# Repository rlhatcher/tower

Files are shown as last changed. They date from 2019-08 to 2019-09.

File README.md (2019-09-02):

# Launch Tower
This is a (mostly) printed Launch Tower for model rockets. The length is 1m, which is _not_ optimal (1.5m would be best) but the tubes I wanted to use come in 1m or 2m lengths so ...

Rather than work through the complications of desinging an adjustable tower, different size rockets can be accomodated by printing approriate sized upper and lower mounts. 15mm and 20mm body diameter .STLs are provided along with the source [Fusion 360 design file](https://github.com/rlhatcher/tower/blob/master/Tower%20Launcher.f3d?raw=true) where the parameters can be easilly adjusted for any size.

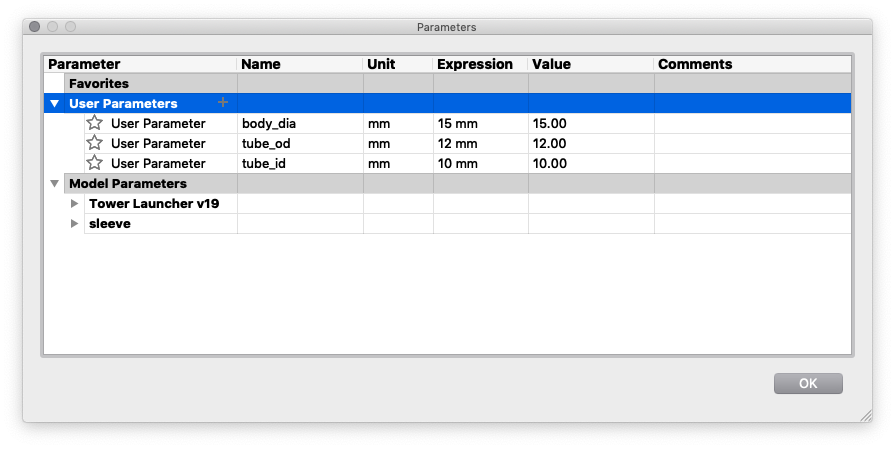
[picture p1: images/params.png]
Parameters


The original design had printed "pegs" on the bottom mount, which promptly bronke on the first attempted use. In hindsight, breaking was inevitble due to the printing orientation so the revied design uses wooden dowels instead. As is often the case, this led to another problem in that 10mm dowelling is _impossible_ to source locally so 8mm dowel with a printed "sleeve" to bring the OD to 10mm and prvide a sung fit with the tubes.



## Ingredients

### Printed

* 3X legs
* Base plate
* 3X dowell sleeves
* Lower mounting plate
* Upper mounting sleeve

### Non-printed

* 3X 8mm multi-groove dowel (40mm long)
* 3X Carbon fibre tubes 12mmx10mmx1m [like these](https://www.easycomposites.co.uk/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)
 
# Assembly

Start with the three legs and the base 

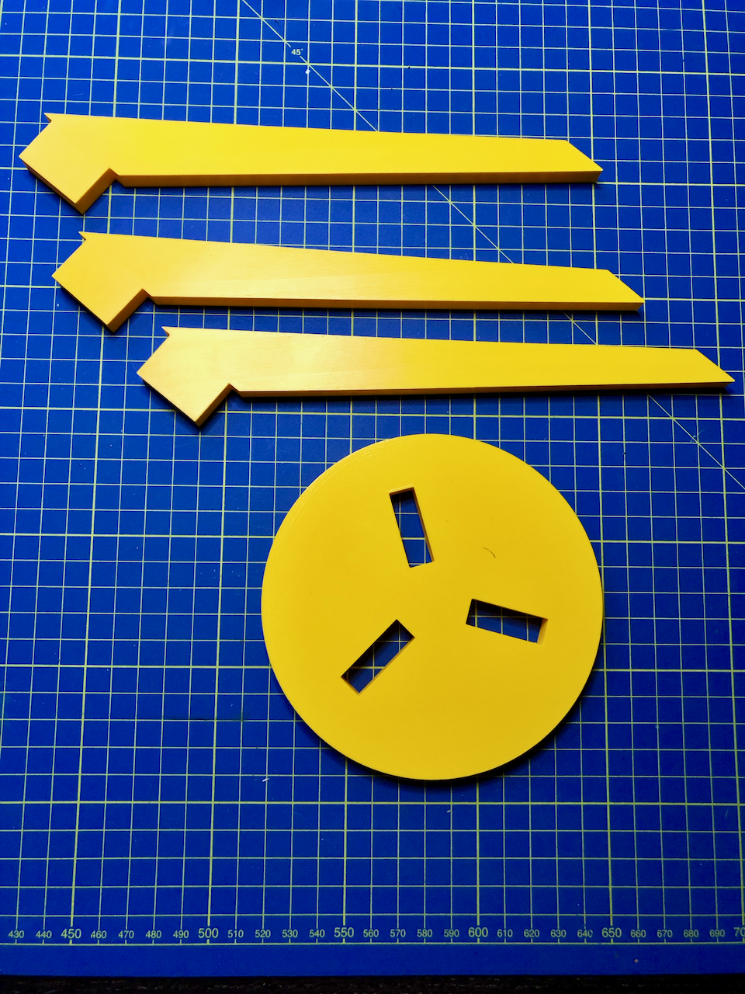
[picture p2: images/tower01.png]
Base


Simply snap the legs throguh the base

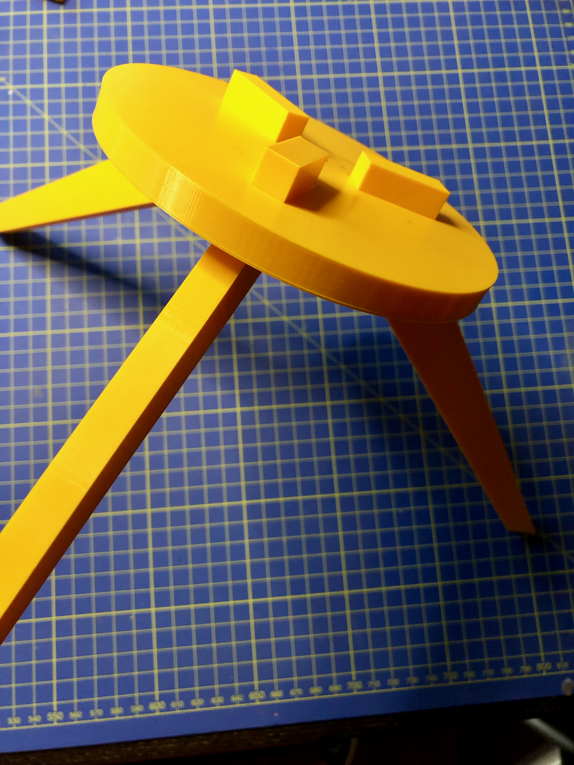
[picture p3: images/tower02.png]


Take the lower mounting plate

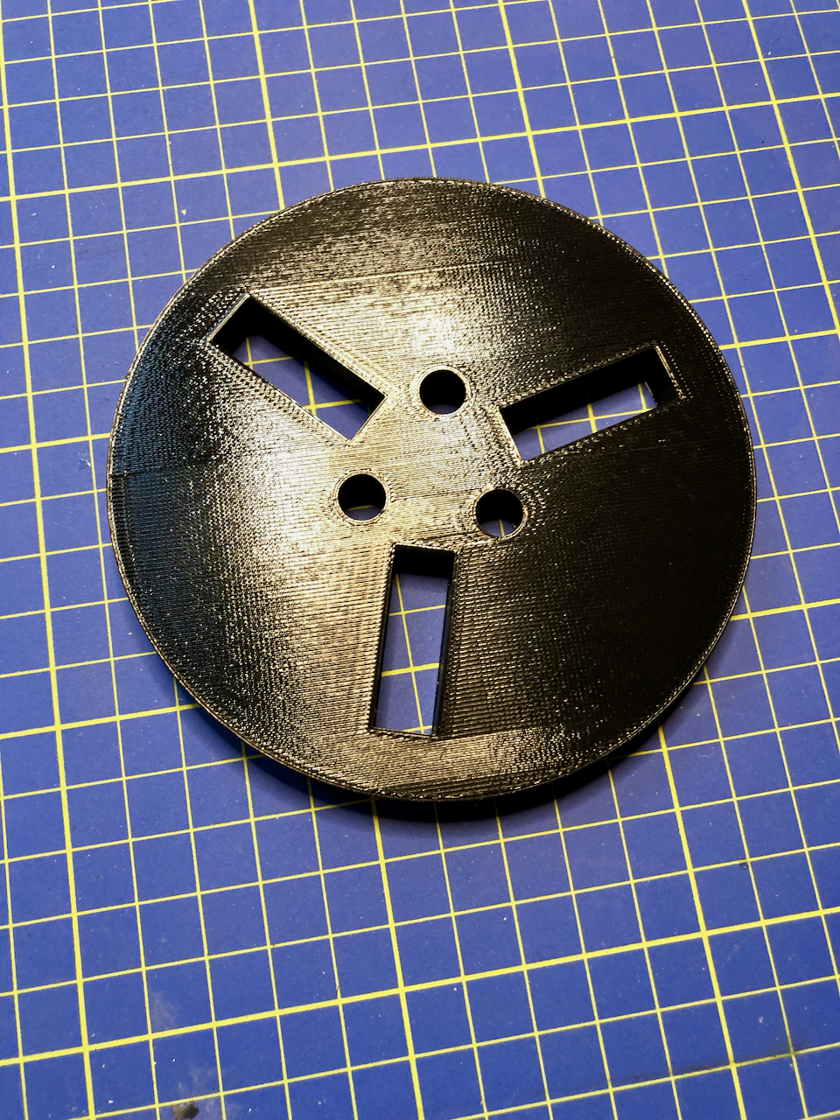
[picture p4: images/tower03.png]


Snap the mounting plate to the base usoing the "lugs" of the legs

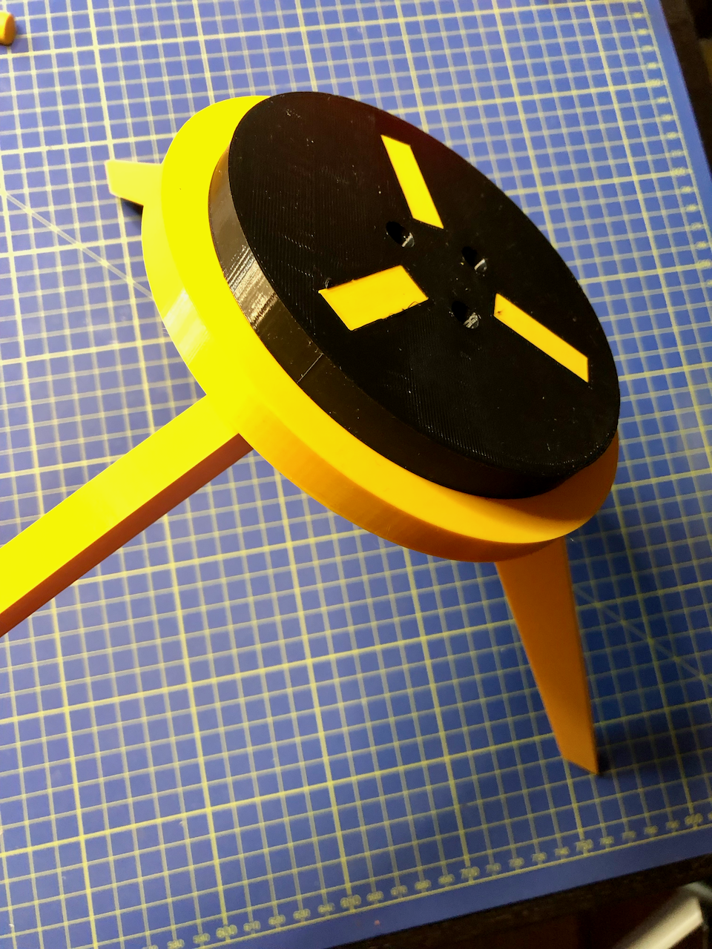
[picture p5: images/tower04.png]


Insert the 40mm dowels

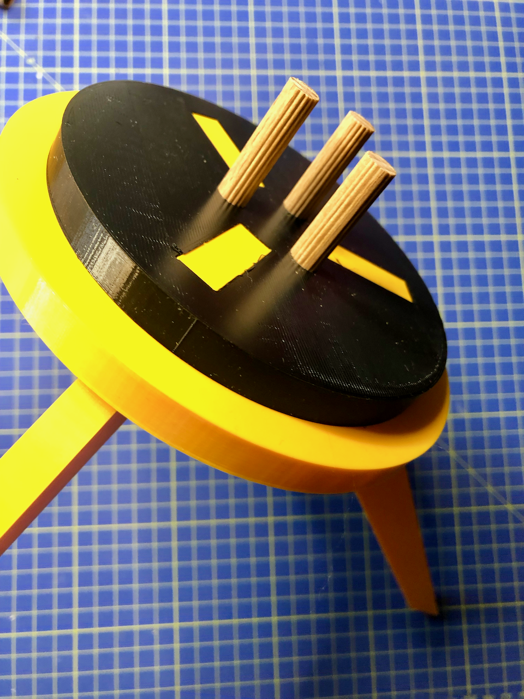
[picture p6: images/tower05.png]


And slip the sleeves over the dowels

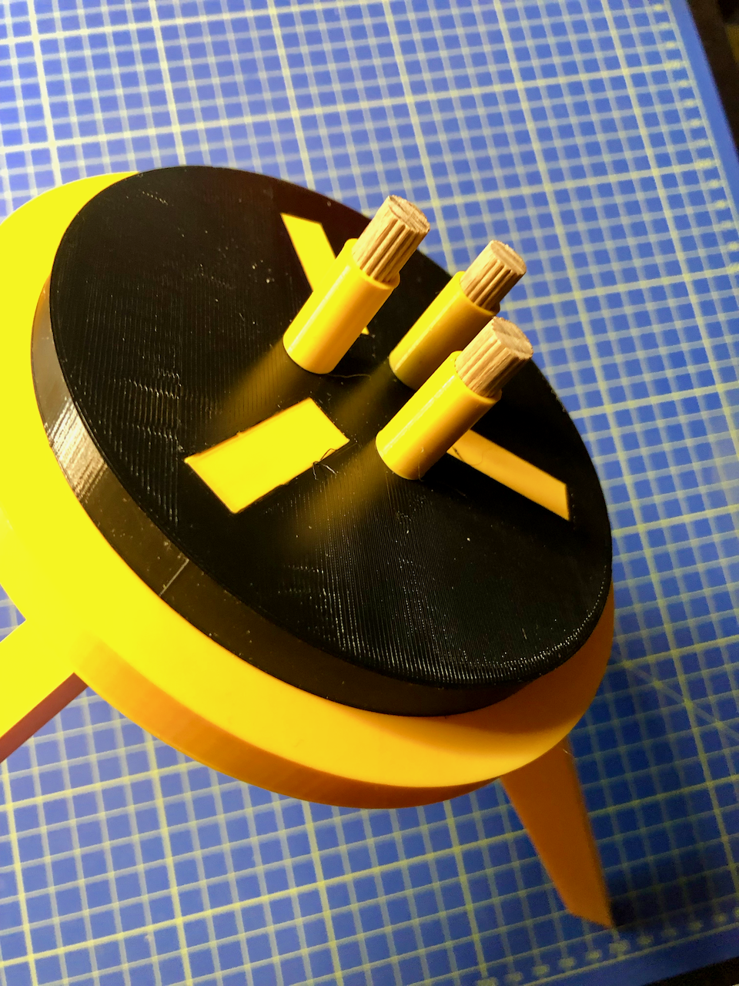
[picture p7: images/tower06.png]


The upper mounting plae has "pegs" printed in (since there is very little stress at. that point)

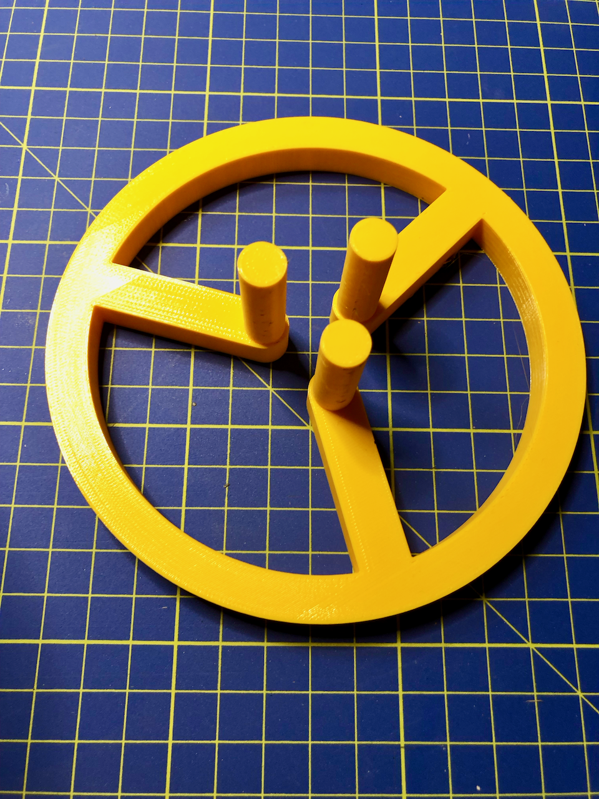
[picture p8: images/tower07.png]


Slip the tubes on to the mounts and you're ready to fly!

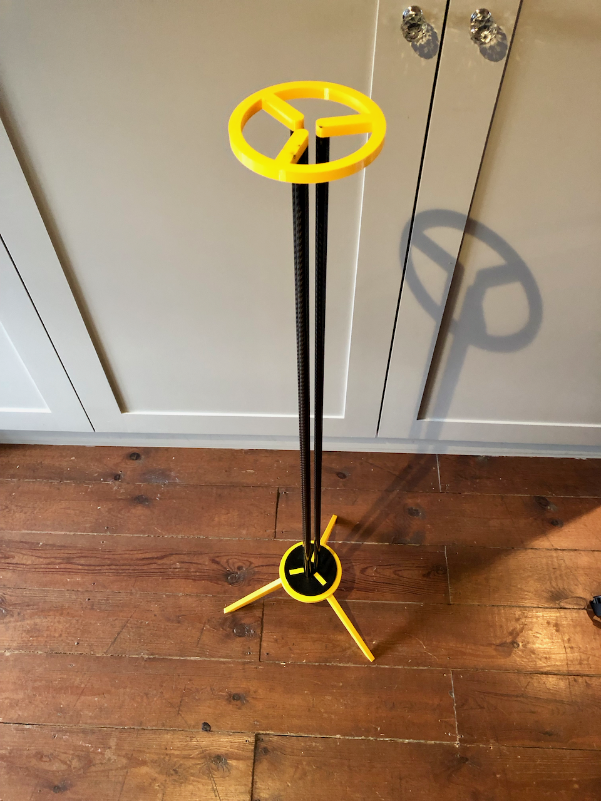
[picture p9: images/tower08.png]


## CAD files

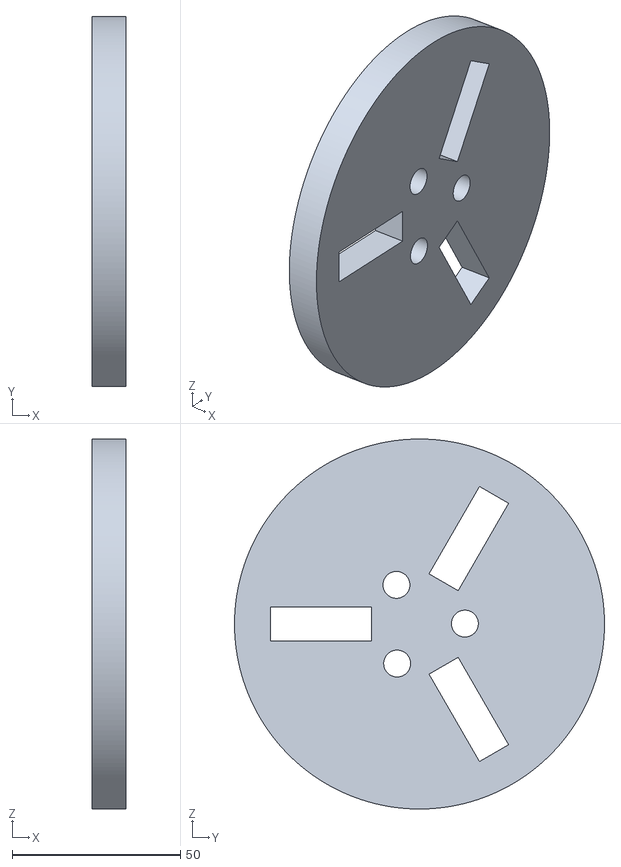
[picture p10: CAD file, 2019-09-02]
mount_lower.stl
10.0 x 110.0 x 110.0

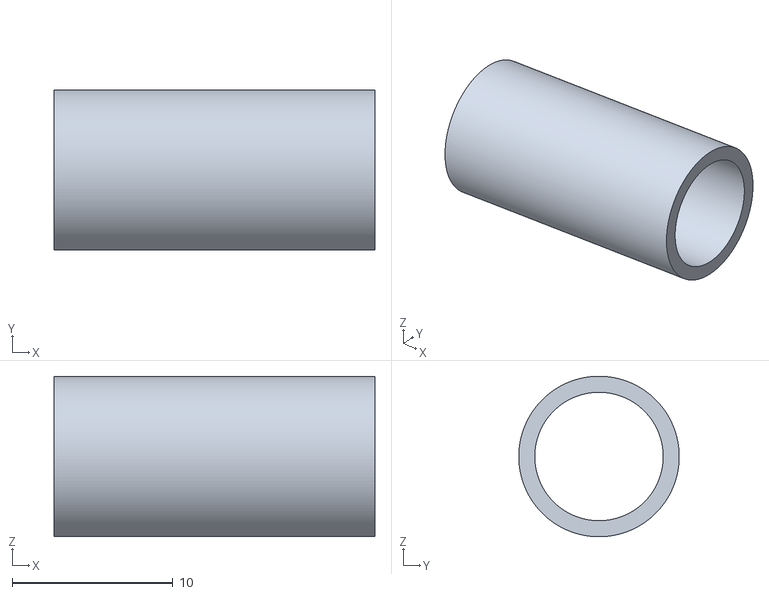
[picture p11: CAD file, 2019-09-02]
sleeve.stl
20.0 x 10.00 x 10.00

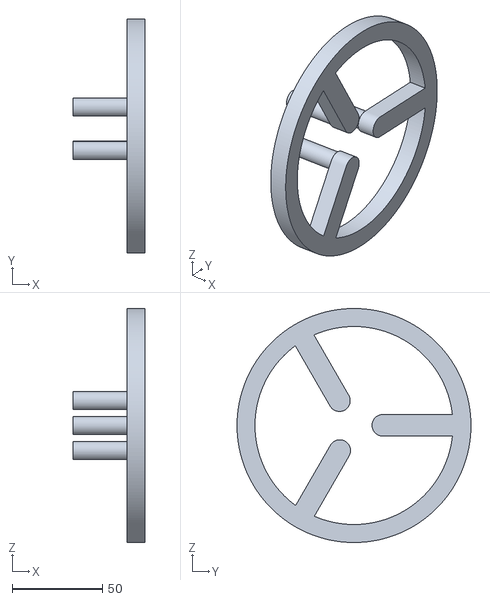
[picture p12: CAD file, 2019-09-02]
mount_upper_20mm.stl
40.0 x 130.0 x 130.0

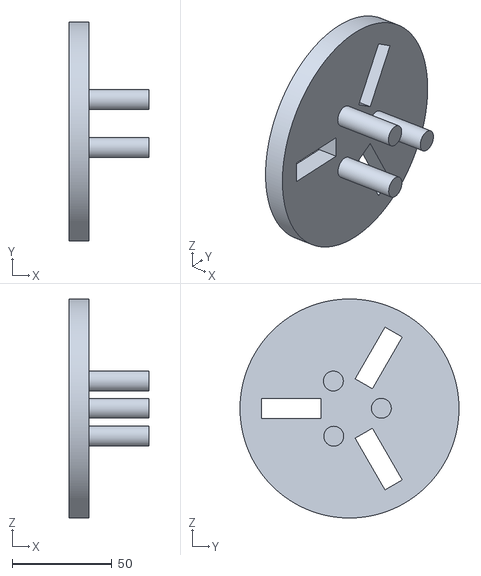
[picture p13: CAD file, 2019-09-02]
mount_lower_20mm.stl
40.0 x 110.0 x 110.0

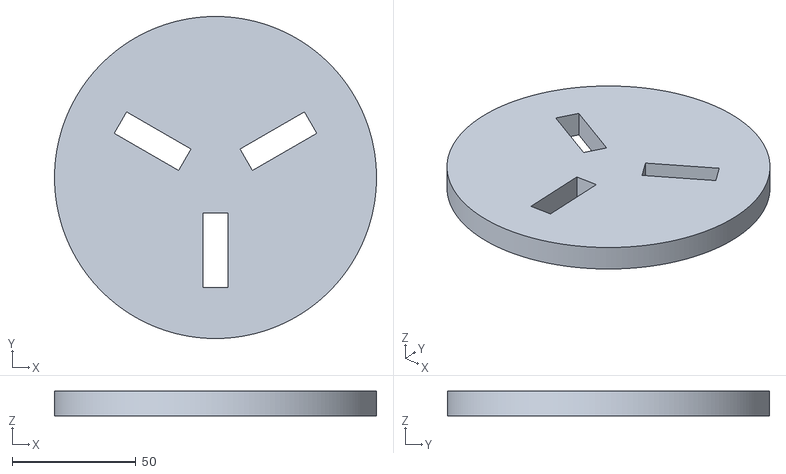
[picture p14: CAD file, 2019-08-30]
base.stl
130.0 x 130.0 x 10.0

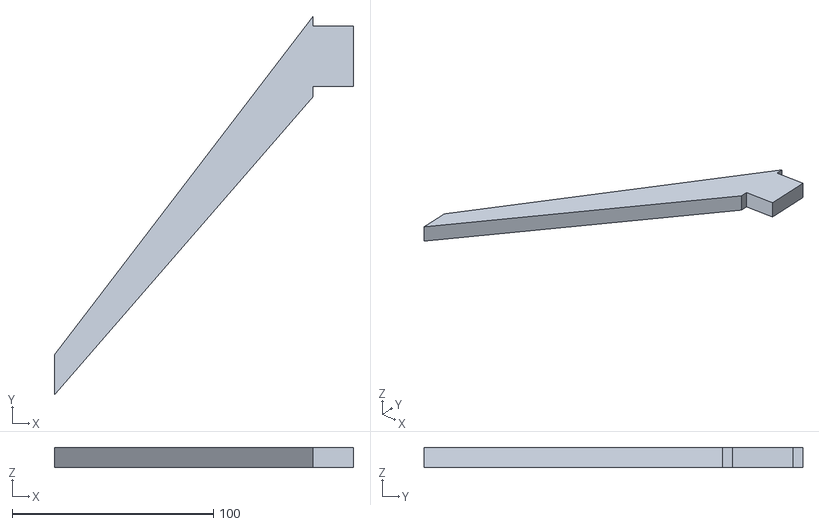
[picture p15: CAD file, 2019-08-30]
leg.stl
148.6 x 188.2 x 10.0

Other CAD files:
mount_upper.stl
Tower Launcher.f3d

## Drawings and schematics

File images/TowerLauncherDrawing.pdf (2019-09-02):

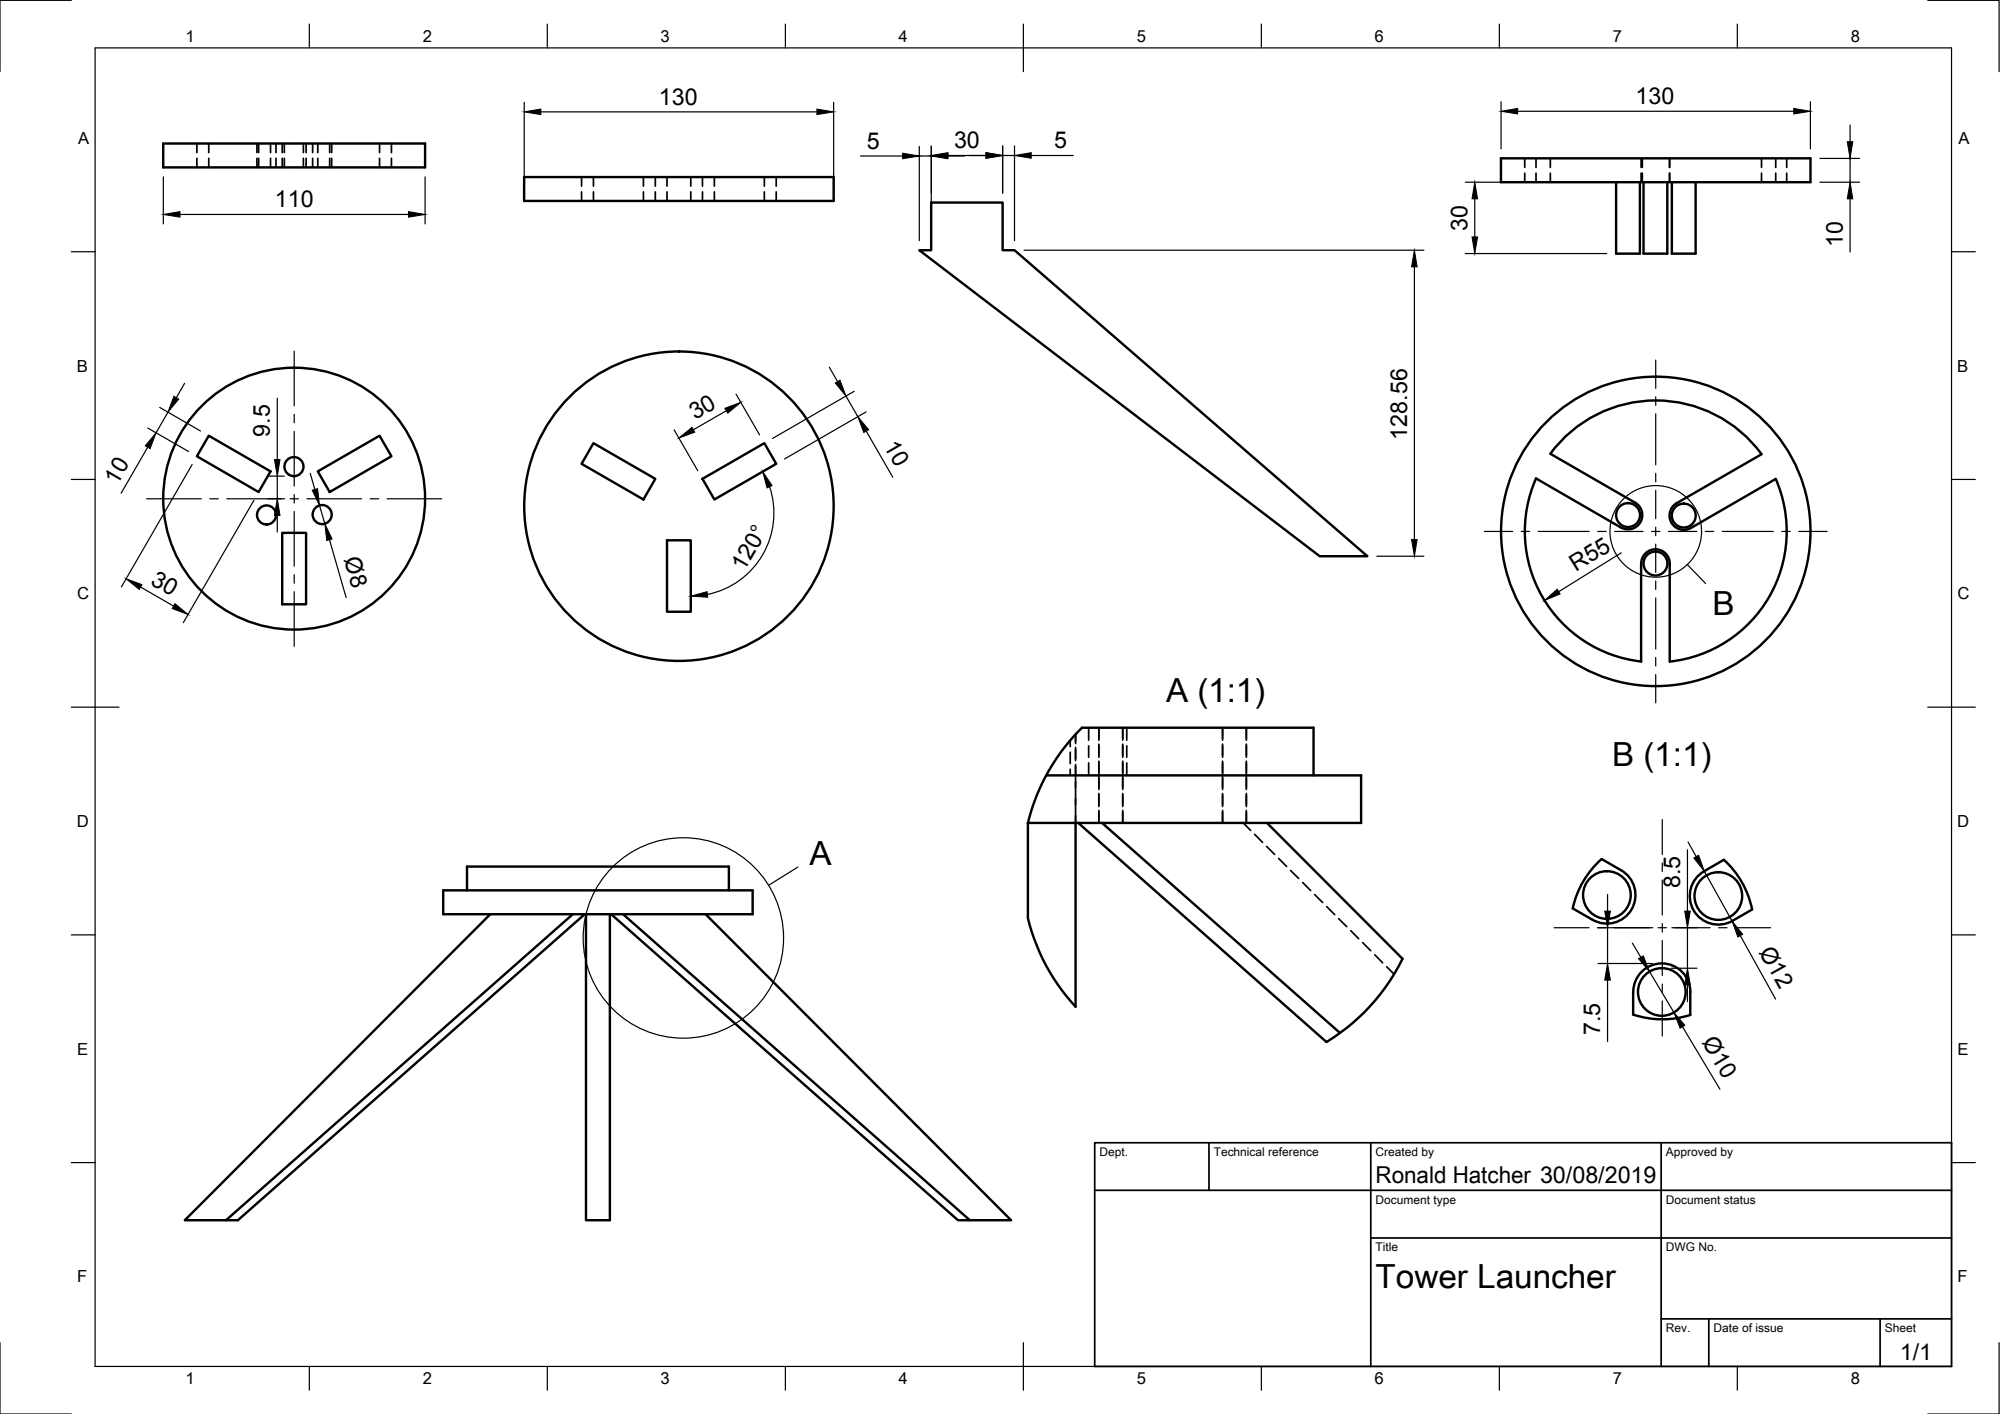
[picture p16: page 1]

Dept. | Technical reference | Created by Ronald Hatcher 30/08/2019 | Approved by

Document type | Document status

Title Tower Launcher | DWG No.

Rev. | Date of issue | Sheet 1/1
